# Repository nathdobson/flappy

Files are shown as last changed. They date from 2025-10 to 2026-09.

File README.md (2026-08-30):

# A 3d-printed Split Flap Display

This project is a redesign of David
Kingsman's [Split Flap Display](https://www.printables.com/model/69464-split-flap-display). See also the [product page](https://burntoutbakery.shop/).

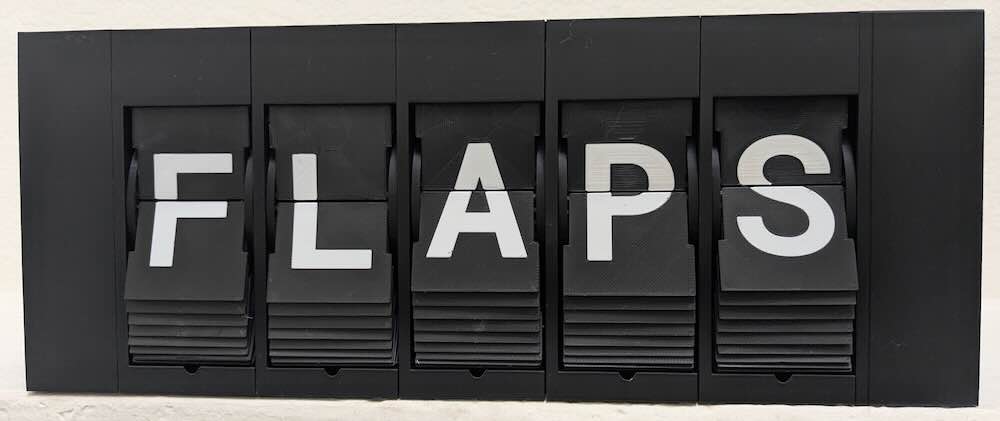
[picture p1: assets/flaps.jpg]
Split Flap Photo


## How it works

This display shows a sequence of symbols in individual 3d-printed modules. Each module contains a drum with flaps
displaying individual symbols. This is similar to a rolodex, except each symbol is split across the front of one flap
and the back of another flap. A motor rotates the drum to change from one symbol to another.

A client (e.g. [this webpage](https://flappy-7d77d.web.app/www)) sends messages to the microcontroller (MCU)
over [MQTT](https://mqtt.org/), a standardized publish/subscribe message protocol designed for IOT devices. Once the MCU
receives a message, it communicates with a series of daisy-chained motor driver circuit boards on the back of each
module. Each driver contains one shift register for controlling a unipolar stepper motor and one shift register for
reading a digital hall effect sensor. Each motor spins until a magnet on the drum activates the hall sensor, indicating
that the drum is at a particular absolute orientation. The motor then spins a specific number of steps to reach the
desired symbol.

## Prerequisites

Building this project from scratch requires a specific set of equipment and skills.

### Equipment

* Required

    * 3D printer with multi-material support (e.g. Bambu Labs A1 mini with AMS [^2]).
    * Device with a USB port capable of running Chrome.
    * [Soldering iron with temperature adjustment](https://www.amazon.com/Soldering-Digital-Welding-Portable-Electric/dp/B08R3515SF?th=1)
      for assembling boards and pushing Ruthex inserts into 3D printed parts.
    * Wire cutters
    * Wire strippers
    * Pliers
    * Allen wrenches

* Recommended

    * ["Dupont" crimping tool](https://www.amazon.com/IWISS-SN-28B-Crimping-AWG28-18-Dupont/dp/B00OMM4YUY?th=1) for
      assembling cables.
    * Multimeter for basic connection and voltage tests.

* Potentially useful
    * Laptop with at least 32GB of RAM for rendering models.
    * Oscilloscope for debugging serial communications.

### Skills

* Required
    * Soldering through-hole components
    * Crimping custom cables
* Recommended
    * The Rust programming language
    * Basic embedded software development
    * Basic understanding of CAD
    * Basic 3D printing debugging skills
    * Basic digital circuit design

## Bill of Materials

| Name of Part | Quantity per display | Quantity per letter | 
|---|---|---|
| [Raspberry Pi Pico 2 W MCU with headers](https://www.adafruit.com/product/6328) | 1 | |
| 12v power supply (at least 250mA per character) | 1 | |
| [Adafruit 12v to 5v converter](https://www.adafruit.com/product/5882) | 1 | |
| [Custom motor driver circuit board](https://github.com/nathdobson/flappy/tree/main/driver) | | 1 |
| [28BYJ-48 12v motor](https://www.amazon.com/Podazz-4-Phase-5-Line-Stepper-28BYJ-48/dp/B0DCFV3C2C) | | 1 |
| [KY-003 hall sensor module](https://www.amazon.com/Ransanx-Magnetic-KY-003-3-3V-5V-Pressure/dp/B0F32N1LHX?th=1) | | 1 |
| [PLA (background color)](https://us.store.bambulab.com/products/pla-basic-filament) | ~132 g | ~217 g |
| [PLA (foreground/text color)](https://us.store.bambulab.com/products/pla-basic-filament) | | ~18 g |
| [PETG](https://us.store.bambulab.com/products/petg-hf) for stacked prints (optional) | | ~30 g |
| Ruthex M2 inserts | 4 | 8 |
| Ruthex M3 inserts | 4 | 6 - 8 |
| [M2 x 6mm button head screws](https://www.amazon.com/dp/B0CNQXP56N?th=1) | 4 | 6 |
| [M2 x 10mm button head screws](https://www.amazon.com/dp/B0CNQVP8CC?th=1) | | 2 |
| [M3 x 6mm button head screws](https://www.amazon.com/dp/B0DNMZWZZV?th=1) | | 6 |
| [6mm x 2mm disc magnets](https://www.amazon.com/dp/B0CZ71S57Y?ref=ppx_yo2ov_dt_b_fed_asin_title&th=1) for drum | | 1 |
| Assorted dupont crimps, housings, and pin headers | | |
| [26 AWG UL1061 stranded wire](https://www.remingtonindustries.com/hook-up-wire/hook-up-wire-26-awg-ul1061-stranded-kit-2-color-sets-2-spool-sizes-available) for hall sensor cables | | |
| Assorted solid wire for manually soldered boards | | |
| Assorted stranded wire for cables | | |

## Repository structure

The repository is divided into several hardware and software components:

* [common/](common/) A cargo workspace with utilities and configuration in use by several components
* [driver/](driver/) A KiCad PCB design for the motor driver attached to each character.
* [firmware/](firmware/) A cargo workspace with the firmware for the Raspberry Pi Pico 2 W.
* [models/](models/) A cargo crate with binaries that generate .3mf files for each 3D-printed part.
* [native-client/](native-client/) A cargo workspace with a binary for configuring the display over USB or Bluetooth.
* [spindle/](spindle/) A cargo workspace with a simple scripting language for controlling the display.
* [submodules/](submodules/) A set of git submodules with forks of dependencies.
* [submodules/patina-rs](submodules/patina-rs/) A CAD library for generating 3D meshes from SDFs (signed distance
  functions).
* [web-client](web-client/) A WASM web application for interacting with the display.

## Instructions

### Hardware

1. Download the [latest release](https://github.com/nathdobson/flappy/releases/latest).
1. Order driver PCBs with JLCPCB:
    * `driver-jlcpcb-GERBER.zip` for producing the raw boards.
    * `driver-jlcpcb-BOM.csv` for ordering parts.
    * `driver-jlcpcb-CPL.csv` for placing and assembling parts.
1. For each module, print one each of the following:
    * `model-housing.3mf`: An enclosure for the module.
    * `model-inner.3mf`: The inner half of the drum.
    * `model-outer.3mf`: The outer half of the drum.
    * `model-flaps.3mf`: All flaps, stacked with PETG support. Ensure you have flow ratios tuned correctly for all
      filaments. This is effectively a 100% infill print, so overextrusion will ruin the top flaps. Underextrusion of
      the PLA will result in noticeable gaps. Underextrusion of the PETG support will ruin the surface quality of the
      PLA as it sinks into the gaps.
2. For each display, print one of the following:
    * `model-left-cap.3mf`: The cap for the left side of the display, where the motherboard goes.
    * `model-right-cap.3mf`: The cap for the right side of the display.
1. Press M2 and M3 Ruthex threaded inserts into the prints with a soldering iron.
1. Glue magnets into the inner drums. Ensure magnets are in the appropriate orientation for your sensors.
1. Connect inner and outer drums with screws.
1. Insert flaps into drum. PLA flaps should bend enough to fit in. Aligning the first letter with the magnet will
   simplify later calibration.
1. [Important] Remove the pull-up resistor or pull-up LED from the sensors[^1]. This is easy with flush cutters.
1. Route the motor and sensor cables through housings.
1. Connect all cables.
1. Connect the motors, sensors, and drivers to the housings with M2 and M3 screws. Ensure the motor tabs are properly
   centered on the supports.
1. Press the drum assemblies onto the motor axle. Ensure all flaps are pointed clockwise so they won't jam as the drum
   assembly rotates counter-clockwise.

### Software

1. Set up an MQTT broker (e.g. with https://www.emqx.com/).
1. Install the firmware by loading the [setup tool](https://flappy-7d77d.web.app/www/?tab=setup) in Chrome.
1. Fill out the settings in the setup tool. See [blank.json](native-client/blank.json) for defaults.
1. Enter the MQTT broker details in the [connect tool](https://flappy-7d77d.web.app/www/?tab=setup). You can use the resulting URL to connect to the display.
1. Adjust calibration values until the expected letters appear consistently.

## Controlling the display

### MQTT Protocol

In addition to controlling the display with the website, you may communicate directly with the display over MQTT. Each
display publishes or
subscribes to a set of topics with a common topic prefix.

#### Topic prefix + `"/info"`

The display publishes a `DeviceInfo` message (see [common/protocol/src/setup.rs](common/protocol/src/setup.rs)) on this
topic. This message is retained by the server, so new subscriptions to this topic will immediately receive this message.

#### Topic prefix + `"/request"`

Clients may publish `DisplayRequest` messages (see [common/protocol/src/display.rs](common/protocol/src/display.rs)) on
this
topic. If the display is processing a previous request when a new request arrives, the display cancels the previous
request and starts the new one.

##### `Run` messages

To display a single static message, send a UTF-8 encoded string as follows:

```
{"Run": "helloworld"}
```

The display splits the message into unicode graphemes, then tries to find the best match for each grapheme. The
algorithm accounts for [Unicode Equivalence](https://en.wikipedia.org/wiki/Unicode_equivalence) and capitalization.

##### `RunSpindle` messages

To display a repeating or changing message, send a UTF-8 encoded `spindle` script as follows:

```
{"RunSpindle": "display(\"hi\");sleep_ms(1000);display(\"hi\");"}
```

See the [Spindle](spindle/README.md) documentation for details on the scripting language.

#### Topic prefix + `"/response"`

When the display starts spinning the flaps to a new position, it sends a `Start` message with the content that will
appear. This message may not exactly match the original message due to normalization or capitalization changes.

```
{"Start":["H","E","L","L","O","W","O","R","L","D"]}
```

When the display stops spinning the flaps, it sends an equivalent `Stop` message:

```
{"Stop":["H","E","L","L","O","W","O","R","L","D"]}
```

The stop message is retained, so clients may determine the current contents of the display.

# License
The contents of the [models](models/) and [driver](driver/) directories and associated release artifacts
are licensed under the [CERN-OHL-W license](LICENSE-CERN-OHL-W-2.0). The remainder of this repository
is licensed under the [LGPL v3.0 license](LICENSE-LGPL-3.0).

[^2]: The provided 3MF files are configured for use with BambuStudio and tuned for PLA with PETG support on the Bambu A1 Mini
with AMS. The files will likely work on other slicers and printers, but may require additional tuning.

[^1]: The KY-003 board contains an A3144 digital hall sensor chip. The A3144 has a minimum Vcc of 4.5V and open-collector
active-low digital output. The KY-003 includes a resistor and LED in series to pull-up the output signal to Vcc. This
pull-up means the minimum logic output voltage for the KY-003 is also 4.5V. The
Pico's maximum logic voltage is 3.3V, so it cannot connect to a KY-003 without some extra work. Also, the LED introduces
a
voltage drop, which makes it's use as a pull-up in the first place questionable. Instead, we remove the pull-ups from
the KY-003, provide 12V to Vcc, and add a pull-up resistor to 3.3V on the driver board. Failure to remove the pull-ups
will likely result in damage to the driver boards.

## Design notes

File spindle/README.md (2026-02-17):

# Spindle

Spindle is a simple scripting language for controlling embedded systems.

## Features

* Rust-based syntax
* Imperative control flow
* Dynamic typing
* Reference-counted garbage collection
* [TODO] Incremental heap compaction to limit memory fragmentation
* Does not invoke the [global allocator](https://doc.rust-lang.org/std/alloc/index.html#the-global_allocator-attribute).
* Denial-of-service protection for untrusted scripts.
  * Memory usage limits
  * Compatible with `--cfg no_global_oom_handling`
  * Stack overflow protection
  * [TODO] Execution time budget between yields to the executor
* Compatible with `#![no_std]`.

## Types

* `i64` - a signed 64-bit integer.
* `bool` - false or true
* `null` - a type with the single value `null`
* `string` - a heap reference to a utf-8 encoded string

## Functions

* `display` - concatenates all parameters and show the resulting string on the display,
  returning once the flaps stop spinning.
  ```
  display("HelloWorld");
  ```
* `print` - print a string to the serial console.
* `sleep_ms` - wait for a certain number of milliseconds to pass.
  ```
  display("Hello");
  sleep_ms(1000);
  display("Bye");
  ```

## Language features
* String literals with double quotes: (e..g `"helloworld"`
* Integer literals (e.g. `10`)
* `null` literal
* boolean literals `false` and `true`.
* Arithmetic operators on integers `+`, `-`, `*`, `/`.
* Variables with declarations with `let` statements.
  ```
  let x = 1;
  display(x);
  ```
* `if` and `if`-`else` statements
    ```
    if foo {
        ...
    }
    ```
    ```
    if foo {
        ...
    } else {
        ....
    }
    ```
    ```
    if foo {
        ...
    } else if bar {
        ...
    } else {
        ...
    }
    ```
* `for` range loops (first index is inclusive, second index is exclusive).
    ```
    for x in 0..10 {
        print(x);
    }
    ```

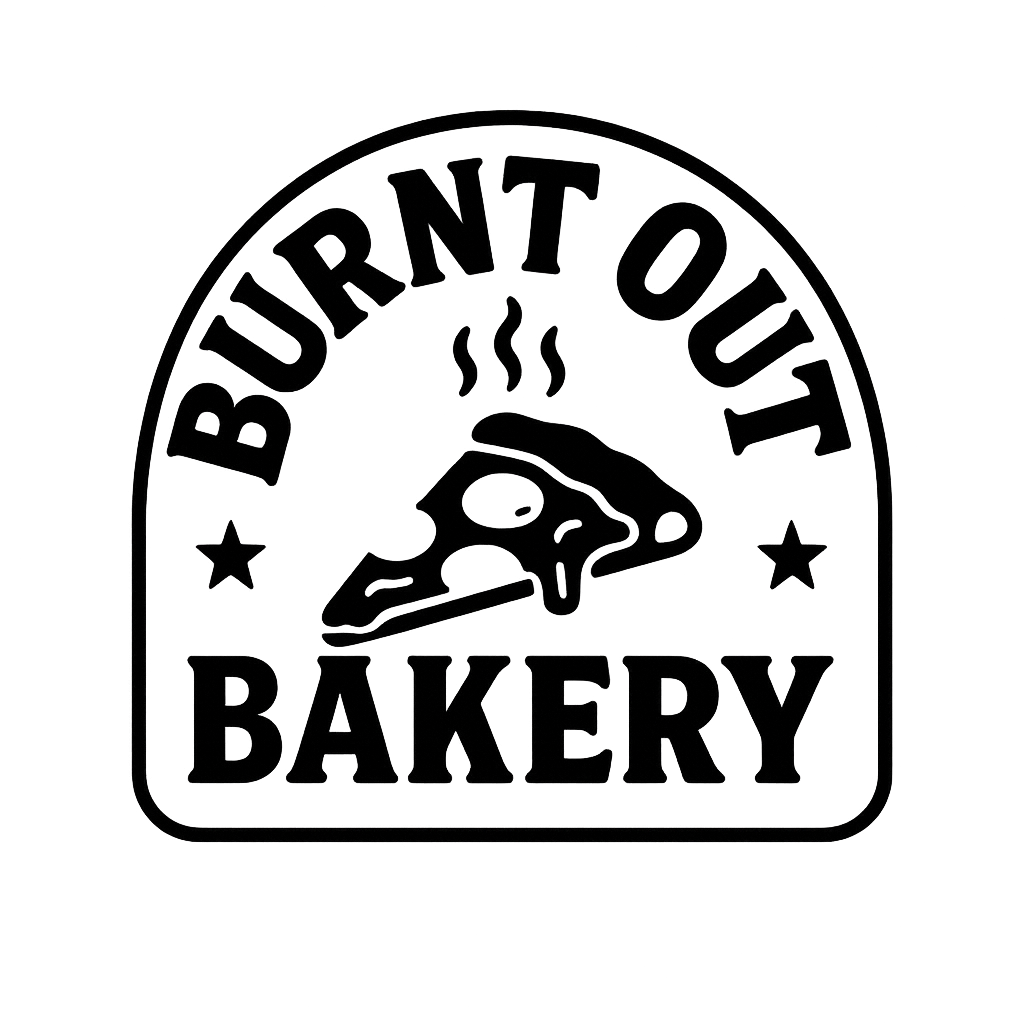
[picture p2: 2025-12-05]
driver/driver-v4/BurntOutBakery/BurntOutBakery.png

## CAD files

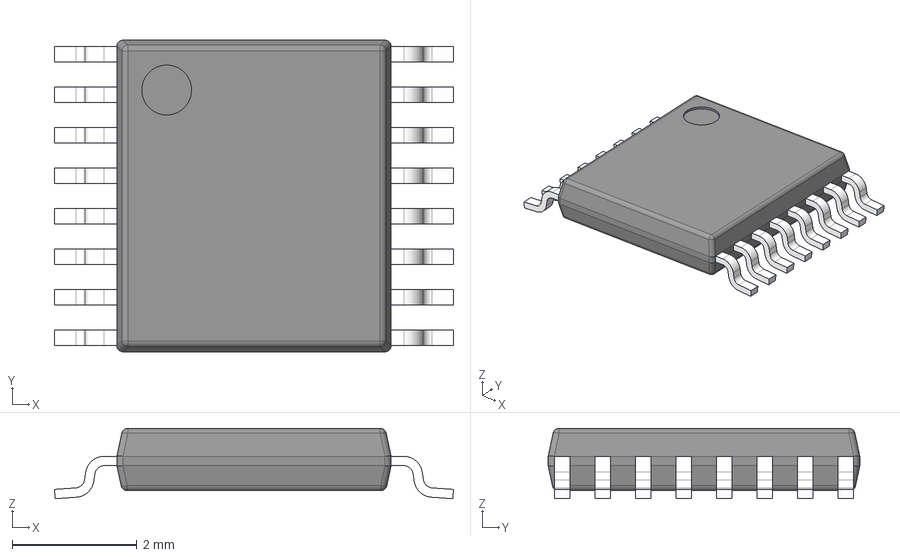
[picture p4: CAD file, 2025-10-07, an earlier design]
driver/driver-v2/ul_DRV8804PWP/PWP0016J.stp
6.40 x 5.00 x 1.13 mm
BODY-TSSOP
LEAD-TSSOP x 16
PIN1
DAP

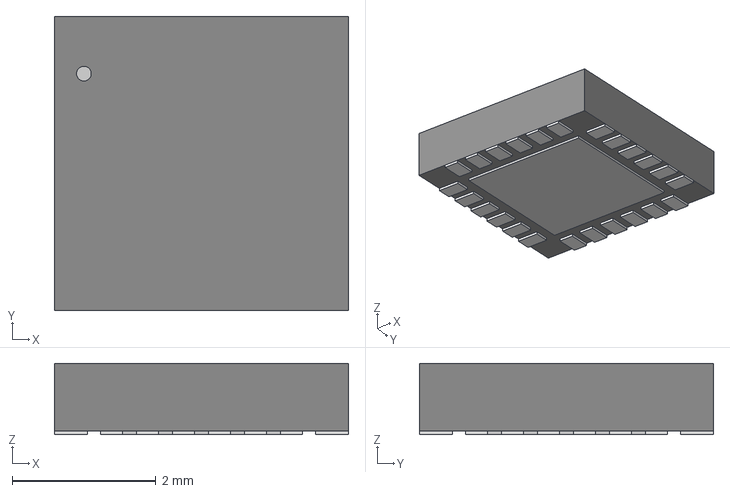
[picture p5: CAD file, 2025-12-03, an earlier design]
driver/driver-v2/ul_MP6605CGR-Z/QFN-24_MP6605C_MNP.step
4.09 x 4.09 x 0.993 mm

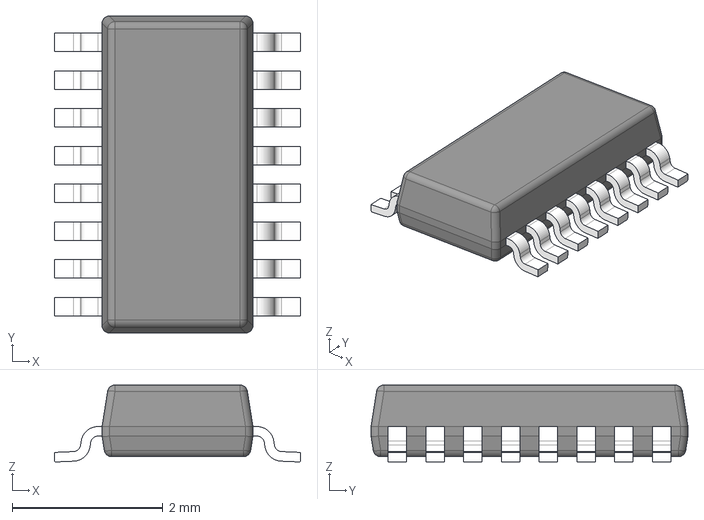
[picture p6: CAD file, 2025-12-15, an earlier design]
driver/driver-v2/ul_SN74HCS165DYYR/DYY0016A.stp
3.26 x 4.20 x 1.02 mm
BODY-TSSOP
LEAD-TSSOP x 16

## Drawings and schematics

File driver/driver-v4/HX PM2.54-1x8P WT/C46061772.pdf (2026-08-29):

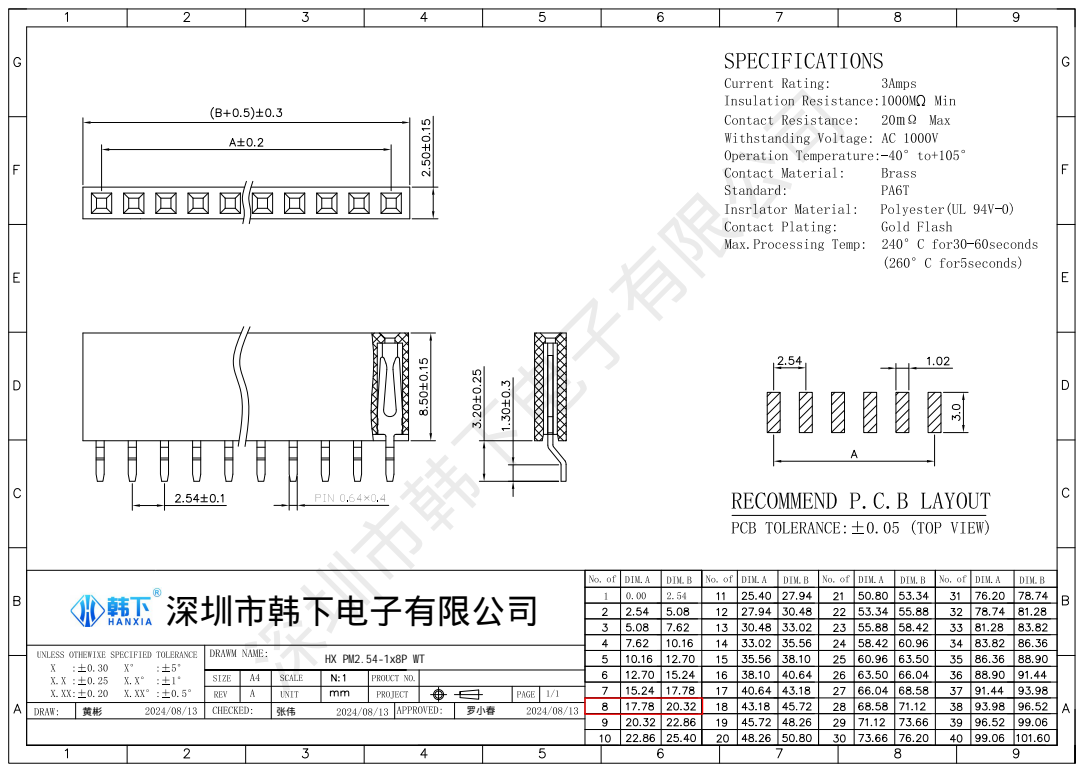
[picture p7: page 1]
深圳市韩下电子有限公司

深圳市韩下电子有限公司 HX PM2.54-1x8P WT 罗小春

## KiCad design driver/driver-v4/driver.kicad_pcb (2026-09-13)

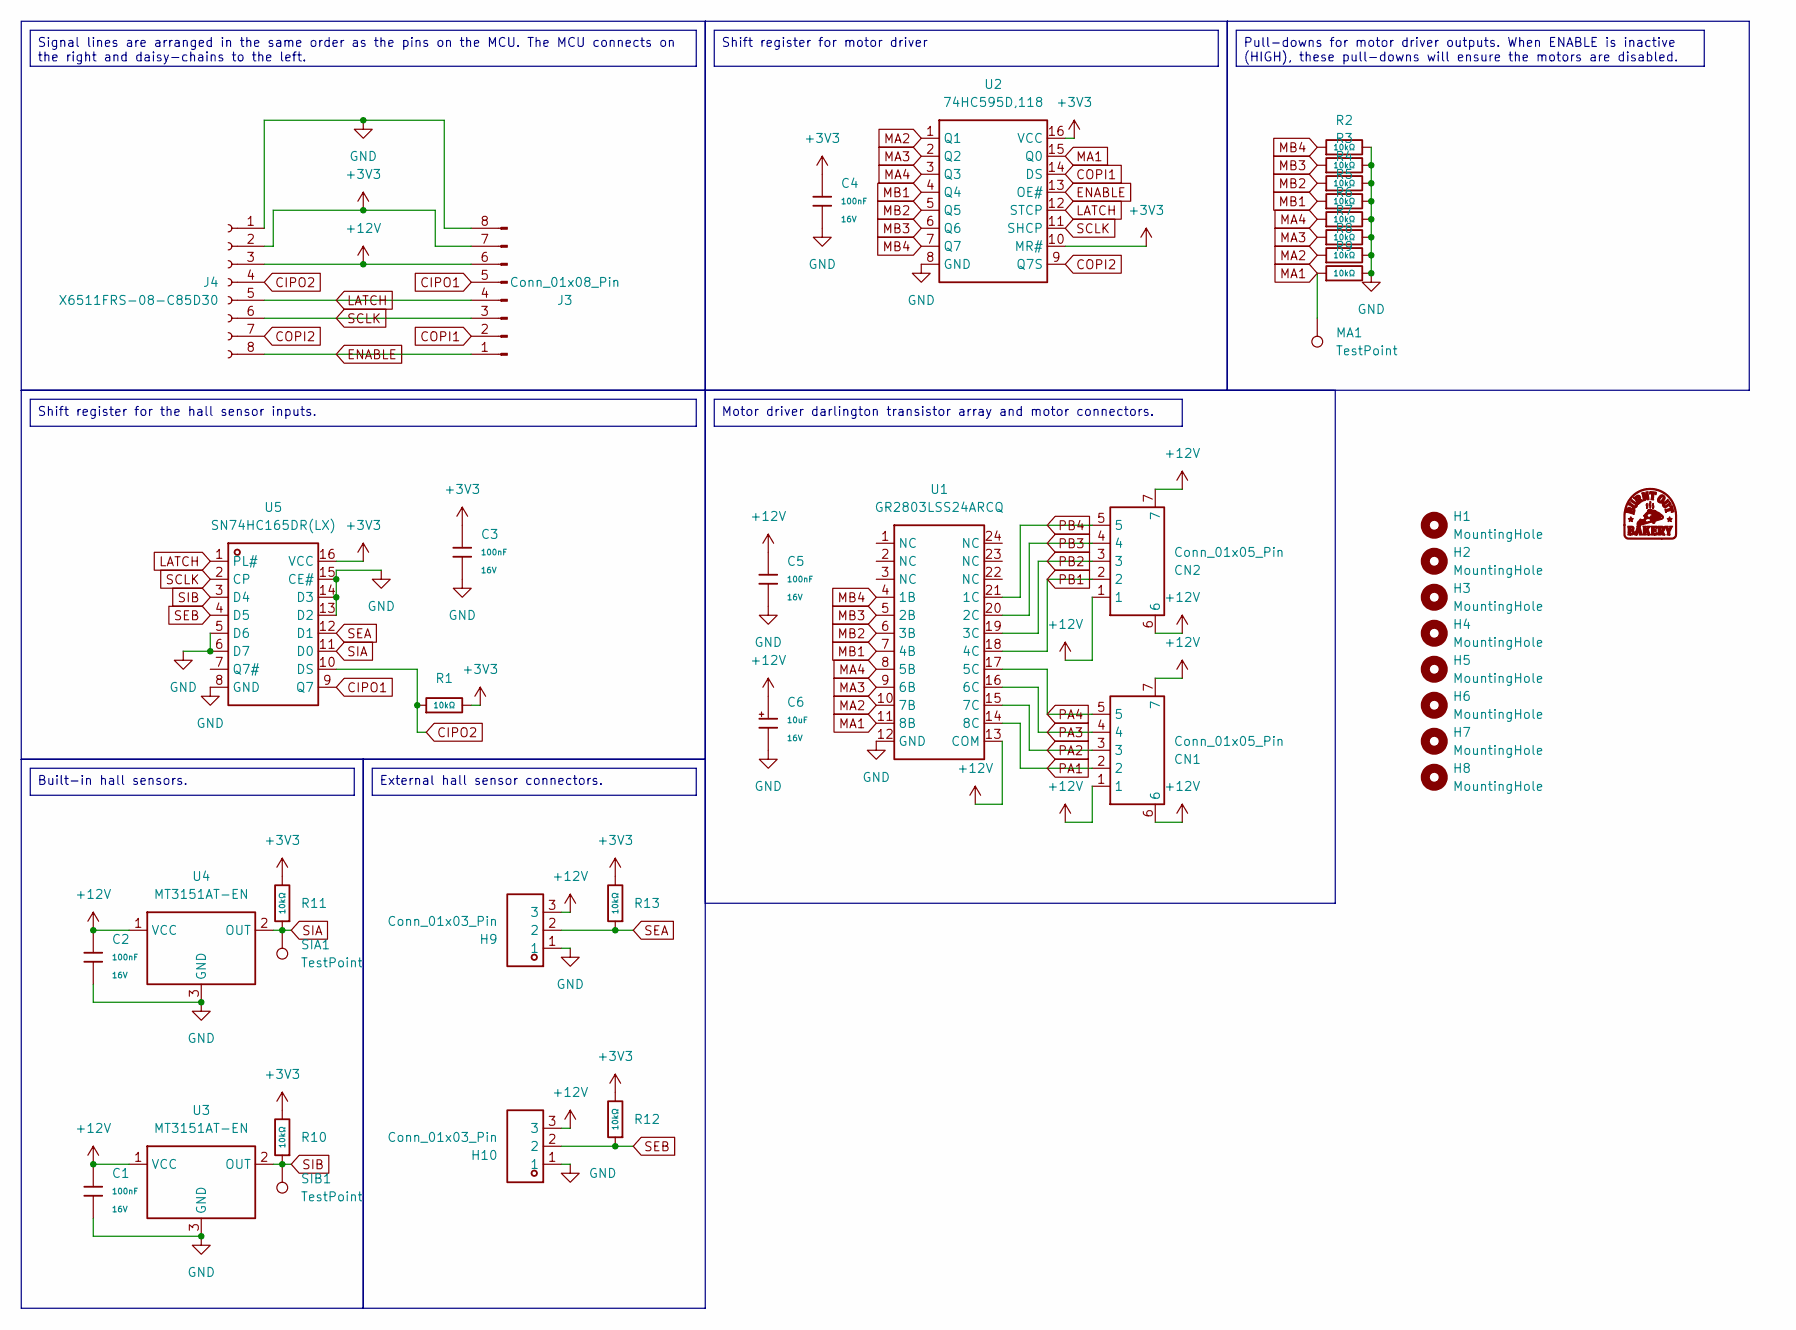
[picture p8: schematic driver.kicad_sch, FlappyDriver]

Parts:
C1, C2, C3, C4, C5: 100nF; C_0402; Voltage Rated 16V; Tolerance ±10%; Part CL05B104KO5NNNC; LCSC C1525
C6: 10uF; C_CASE-A-3216-18(mm); Tolerance ±10%; Rated Voltage 16V; Part TAJA106K016RNJ; LCSC C7171
CN1, CN2: Conn_01x05_Pin; CONN-SMD_5P-P2.50_2.54-5P-LT; Manufacturer Part 2.54-5P-LT; LCSC Part Name 1x5P 间距:2.5mm 立贴 系列:XH
G1: LOGO; BurntOutBakery
H1, H2, H3, H4, H5, H6, H7, H8: MountingHole; MountingHole_2.2mm_M2_ISO14580
H9, H10: Conn_01x03_Pin; HDR-TH_3P-P2.54_DZ254S-11-03-48; Manufacturer Part DZ254S-11-03-48; LCSC Part Name 1x3P 间距:2.54mm 方针 立贴
J3: Conn_01x08_Pin; HDR-SMD_PZ254RS-11-08P-01
J4: X6511FRS-08-C85D30; HDR-SMD_8P-P2.54-H-F-L11.5
MA1: TestPoint; TestPoint_THTPad_D2.0mm_Drill1.0mm
R1, R2, R3, R4, R5, R6, R7, R8, R9, R10, R11, R12, R13: 10kΩ; R_0402; Overload Voltage (Max) 50V; Tolerance ±1%; Part 0402WGF1002TCE; LCSC C25744
SIA1: TestPoint; TestPoint_THTPad_D2.0mm_Drill1.0mm
SIB1: TestPoint; TestPoint_THTPad_D2.0mm_Drill1.0mm
U1: GR2803LSS24ARCQ; SSOP-24_L8.7-W3.9-P0.64-LS6.0-BL; Manufacturer Part GR2803LSS24ARCQ; LCSC Part Name 通道数: 8 集射击穿电压: 25V 集电极电流：500mA 最大输入电压：1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
U2: 74HC595D,118; SOIC-16_L9.9-W3.9-P1.27-LS6.0-BL; Manufacturer Part 74HC595D,118; LCSC Part Name 三态输出 串行至串行或并行移位寄存器
U3, U4: MT3151AT-EN; SOT-23-3_L2.9-W1.3-P1.90-LS2.4-BR; Manufacturer Part MT3151AT-EN; LCSC Part Name 单极检测芯片
U5: SN74HC165DR(LX); SOP-16_L10.0-W3.9-P1.27-LS6.0-BL; Manufacturer Part SN74HC165DR(LX); LCSC Part Name 集成电路

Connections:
+3V3: C3.1, C4.1, J3.7, J4.2, R1.2, R10.2, R11.2, R12.2, R13.2, U2.10 (MR#), U2.16 (VCC), U5.16 (VCC)
+12V: C1.1, C2.1, C5.1, C6.1, CN1.1, CN1.6, CN1.7, CN2.1, CN2.6, CN2.7, H9.3, H10.3, J3.6, J4.3, U1.13 (COM), U3.1 (VCC), U4.1 (VCC)
CIPO1: J3.5, U5.9 (Q7)
CIPO2: J4.4, R1.1, U5.10 (DS)
COPI1: J3.2, U2.14 (DS)
COPI2: J4.7, U2.9 (Q7S)
ENABLE: J3.1, J4.8, U2.13 (OE#)
GND: C1.2, C2.2, C3.2, C4.2, C5.2, C6.2, H9.1, H10.1, J3.8, J4.1, R2.2, R3.2, R4.2, R5.2, R6.2, R7.2, R8.2, R9.2, U1.12 (GND), U2.8 (GND), U3.3 (GND), U4.3 (GND), U5.5 (D6), U5.6 (D7), U5.8 (GND), U5.13 (D2), U5.14 (D3), U5.15 (CE#)
LATCH: J3.4, J4.5, U2.12 (STCP), U5.1 (PL#)
MA1: MA1.1, R9.1, U1.11 (8B), U2.15 (Q0)
MA2: R8.1, U1.10 (7B), U2.1 (Q1)
MA3: R7.1, U1.9 (6B), U2.2 (Q2)
MA4: R6.1, U1.8 (5B), U2.3 (Q3)
MB1: R5.1, U1.7 (4B), U2.4 (Q4)
MB2: R4.1, U1.6 (3B), U2.5 (Q5)
MB3: R3.1, U1.5 (2B), U2.6 (Q6)
MB4: R2.1, U1.4 (1B), U2.7 (Q7)
PA1: CN1.2, U1.14 (8C)
PA2: CN1.3, U1.15 (7C)
PA3: CN1.4, U1.16 (6C)
PA4: CN1.5, U1.17 (5C)
PB1: CN2.2, U1.18 (4C)
PB2: CN2.3, U1.19 (3C)
PB3: CN2.4, U1.20 (2C)
PB4: CN2.5, U1.21 (1C)
SCLK: J3.3, J4.6, U2.11 (SHCP), U5.2 (CP)
SEA: H9.2, R13.1, U5.12 (D1)
SEB: H10.2, R12.1, U5.4 (D5)
SIA: R11.1, SIA1.1, U4.2 (OUT), U5.11 (D0)
SIB: R10.1, SIB1.1, U3.2 (OUT), U5.3 (D4)

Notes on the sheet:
Shift register for the hall sensor inputs.
Signal lines are arranged in the same order as the pins on the MCU. The MCU connects on the right and daisy-chains to the left.
Pull-downs for motor driver outputs. When ENABLE is inactive (HIGH), these pull-downs will ensure the motors are disabled.
Built-in hall sensors.
External hall sensor connectors.
Motor driver darlington transistor array and motor connectors.
Shift register for motor driver

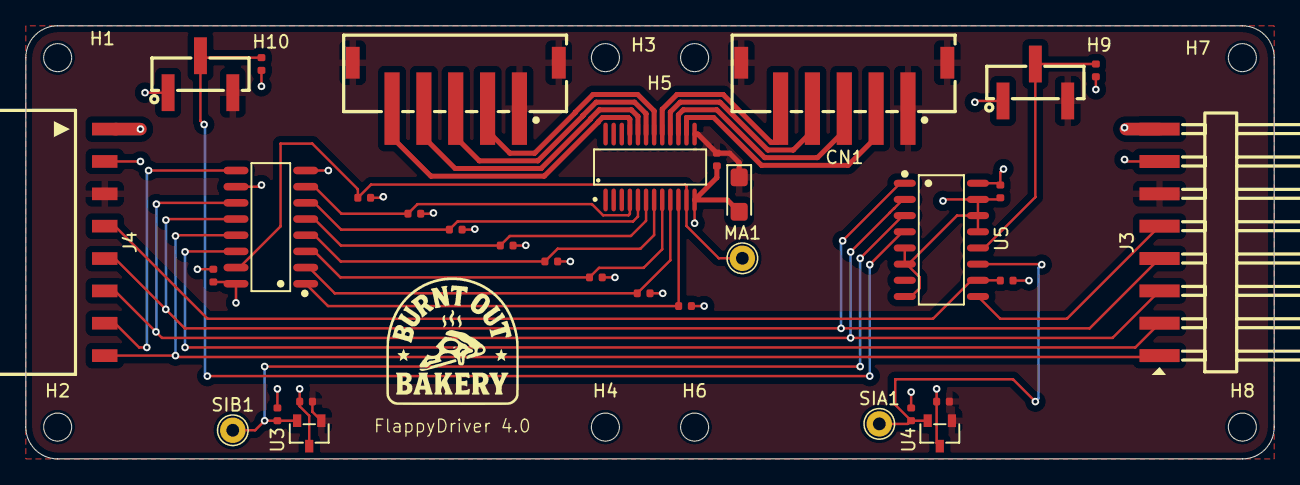
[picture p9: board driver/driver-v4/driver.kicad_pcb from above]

Board: 4 copper layers, 98.0 x 34.0 mm, 42 parts (0 on the bottom side), 30 nets.

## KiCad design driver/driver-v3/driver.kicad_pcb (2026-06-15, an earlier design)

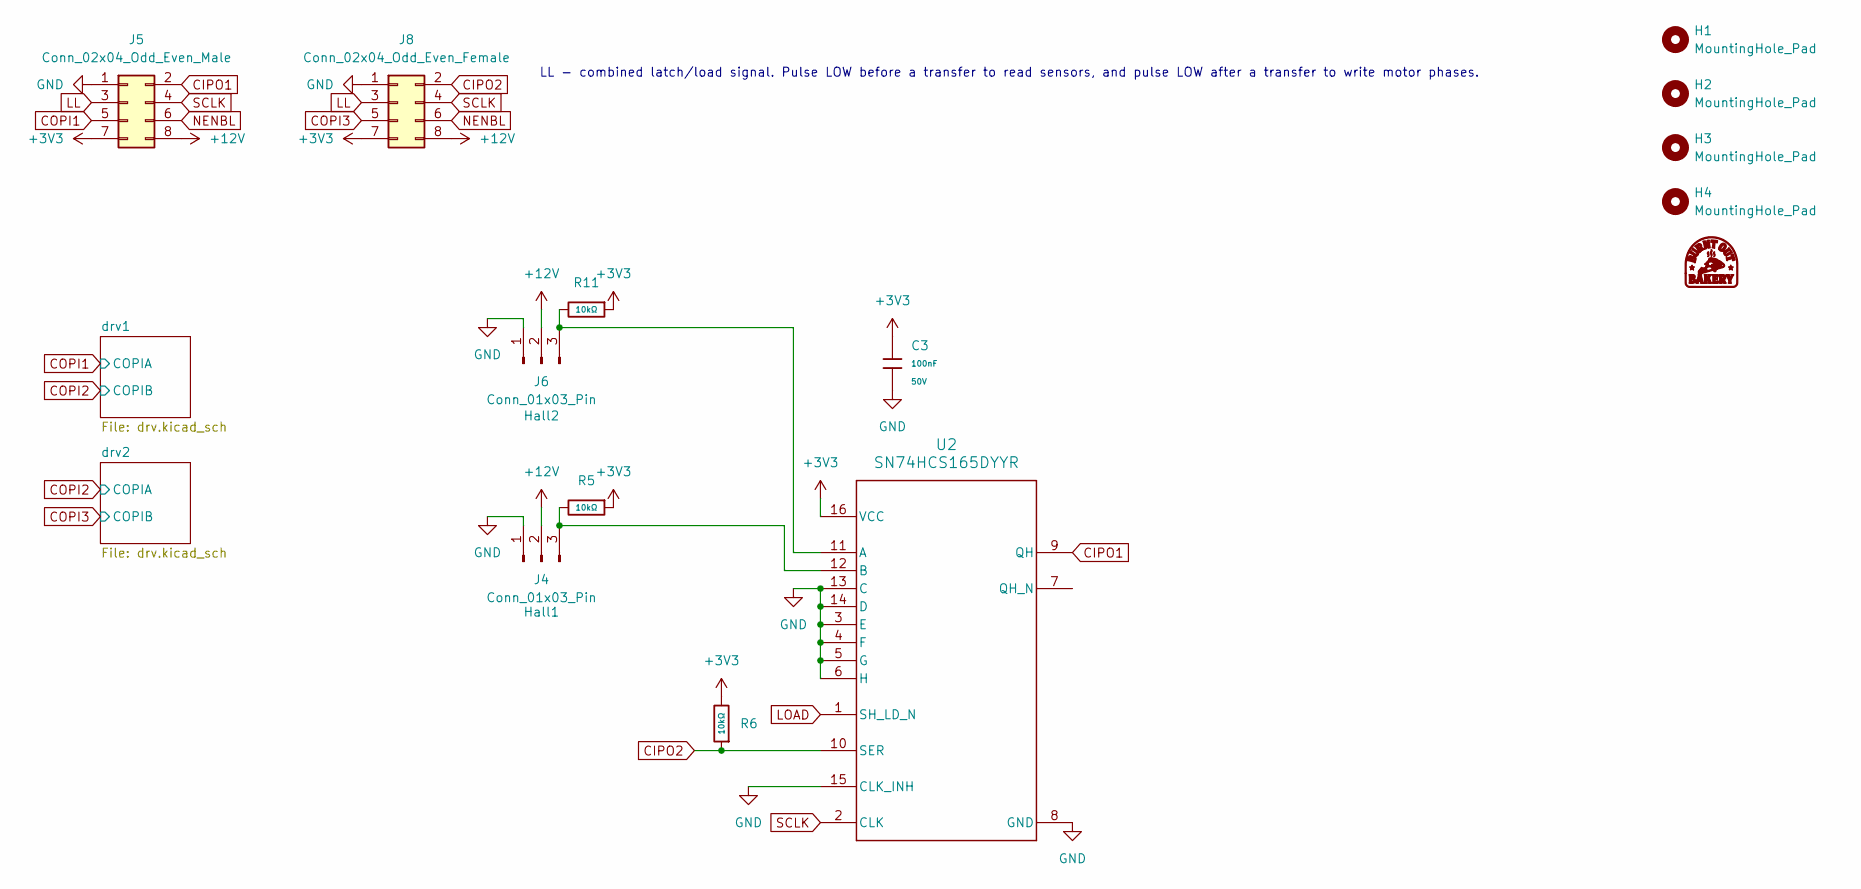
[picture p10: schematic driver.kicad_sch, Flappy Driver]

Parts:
C3: 100nF; C_0603; Voltage Rated 50V; Tolerance ±10%; Part CC0603KRX7R9BB104; LCSC C14663
G1: LOGO; BurntOutBakery
H1, H2, H3, H4: MountingHole_Pad; MountingHole_2.2mm_M2_ISO14580
J4, J6: Conn_01x03_Pin; PinHeader_1x03_P2.54mm_Vertical
J5: Conn_02x04_Odd_Even_Male; PinHeader_2x04_P2.54mm_Horizontal
J8: Conn_02x04_Odd_Even_Female; PinSocket_2x04_P2.54mm_Horizontal
R5, R6, R11: 10kΩ; R_0402; Overload Voltage (Max) 50V; Tolerance ±1%; Part 0402WGF1002TCE; LCSC C25744
U2: SN74HCS165DYYR; DYY0016A-MFG

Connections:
+3V3: C3.1, J5.7, J8.7, R5.1, R6.2, R11.1, U2.16 (VCC)
+12V: J4.2, J5.8, J6.2, J8.8; also elsewhere on the board
CIPO1: J5.2, U2.9 (QH)
CIPO2: J8.2, R6.1, U2.10 (SER)
COPI1: J5.5; also elsewhere on the board
COPI3: J8.5; also elsewhere on the board
GND: C3.2, J4.1, J5.1, J6.1, J8.1, U2.3 (E), U2.4 (F), U2.5 (G), U2.6 (H), U2.8 (GND), U2.13 (C), U2.14 (D), U2.15 (CLK_INH); also elsewhere on the board
LL: J5.3, J8.3
LOAD: U2.1 (SH_LD_N)
NENBL: J5.6, J8.6; also elsewhere on the board
unnamed: J4.3, R5.2, U2.12 (B)
unnamed: J6.3, R11.2, U2.11 (A)
SCLK: J5.4, J8.4, U2.2 (CLK); also elsewhere on the board

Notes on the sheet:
LL - combined latch/load signal. Pulse LOW before a transfer to read sensors, and pulse LOW after a transfer to write motor phases.

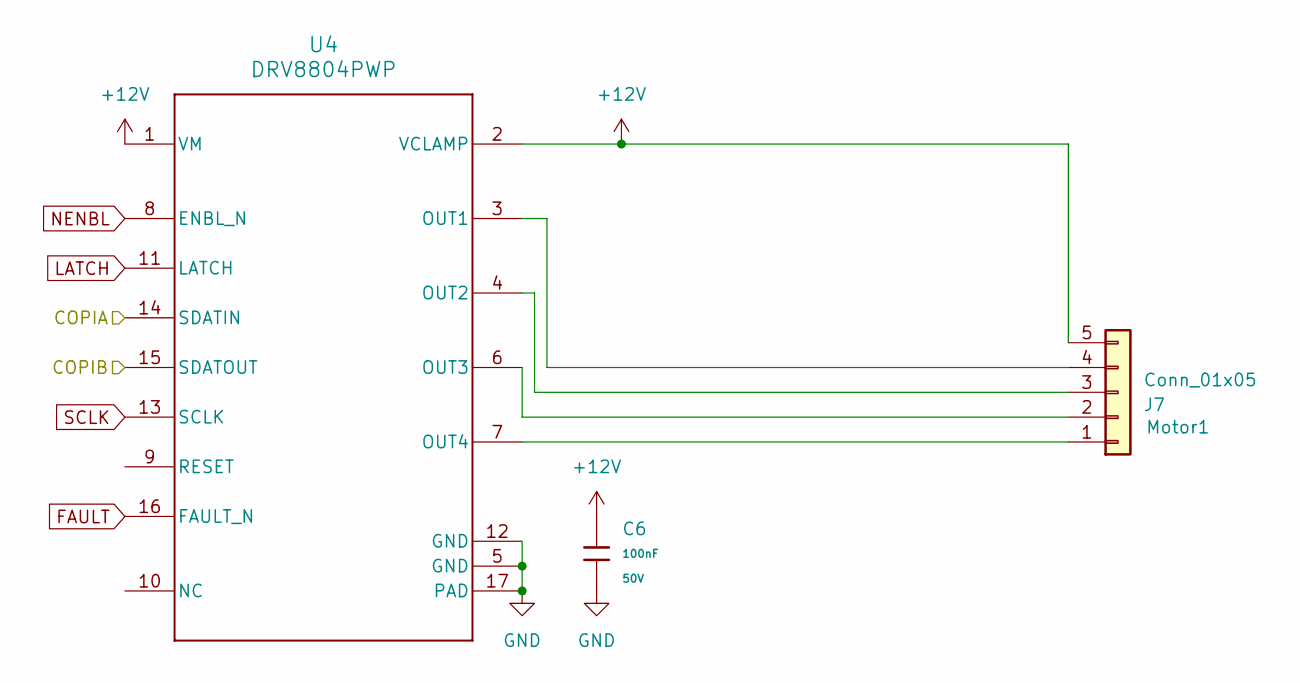
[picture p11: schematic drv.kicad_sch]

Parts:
C6: 100nF; C_0603; Voltage Rated 50V; Tolerance ±10%; Part CC0603KRX7R9BB104; LCSC C14663
J7: Conn_01x05; JST_XH_B5B-XH-A_1x05_P2.50mm_Vertical
U4: DRV8804PWP; HTSSOP-16-1EP_4.4x5mm_P0.65mm_EP3.4x5mm_Mask3x3mm_ThermalVi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

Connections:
+12V: C6.1, J7.5, U4.1 (VM), U4.2 (VCLAMP); also elsewhere on the board
COPI1: U4.14 (SDATIN); also elsewhere on the board
COPI2: U4.15 (SDATOUT); also elsewhere on the board
FAULT: U4.16 (FAULT_N); also elsewhere on the board
GND: C6.2, U4.5 (GND), U4.12 (GND), U4.17 (PAD); also elsewhere on the board
LATCH: U4.11 (LATCH); also elsewhere on the board
NENBL: U4.8 (ENBL_N); also elsewhere on the board
unnamed: J7.1, U4.7 (OUT4)
unnamed: J7.2, U4.6 (OUT3)
unnamed: J7.3, U4.4 (OUT2)
unnamed: J7.4, U4.3 (OUT1)
SCLK: U4.13 (SCLK); also elsewhere on the board

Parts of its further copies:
C1: 100nF; C_0603; Voltage Rated 50V; Tolerance ±10%; Part CC0603KRX7R9BB104; LCSC C14663
J3: Conn_01x05; JST_XH_B5B-XH-A_1x05_P2.50mm_Vertical
U1: DRV8804PWP; HTSSOP-16-1EP_4.4x5mm_P0.65mm_EP3.4x5mm_Mask3x3mm_ThermalVi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

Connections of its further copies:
+12V: C1.1, J3.5, U1.1 (VM), U1.2 (VCLAMP); also elsewhere on the board
COPI2: U1.14 (SDATIN); also elsewhere on the board
COPI3: U1.15 (SDATOUT); also elsewhere on the board
FAULT: U1.16 (FAULT_N); also elsewhere on the board
GND: C1.2, U1.5 (GND), U1.12 (GND), U1.17 (PAD); also elsewhere on the board
LATCH: U1.11 (LATCH); also elsewhere on the board
NENBL: U1.8 (ENBL_N); also elsewhere on the board
unnamed: J3.1, U1.7 (OUT4)
unnamed: J3.2, U1.6 (OUT3)
unnamed: J3.3, U1.4 (OUT2)
unnamed: J3.4, U1.3 (OUT1)
SCLK: U1.13 (SCLK); also elsewhere on the board

Board: 2 copper layers, 20 parts (0 on the bottom side), 23 nets, no tracks yet.

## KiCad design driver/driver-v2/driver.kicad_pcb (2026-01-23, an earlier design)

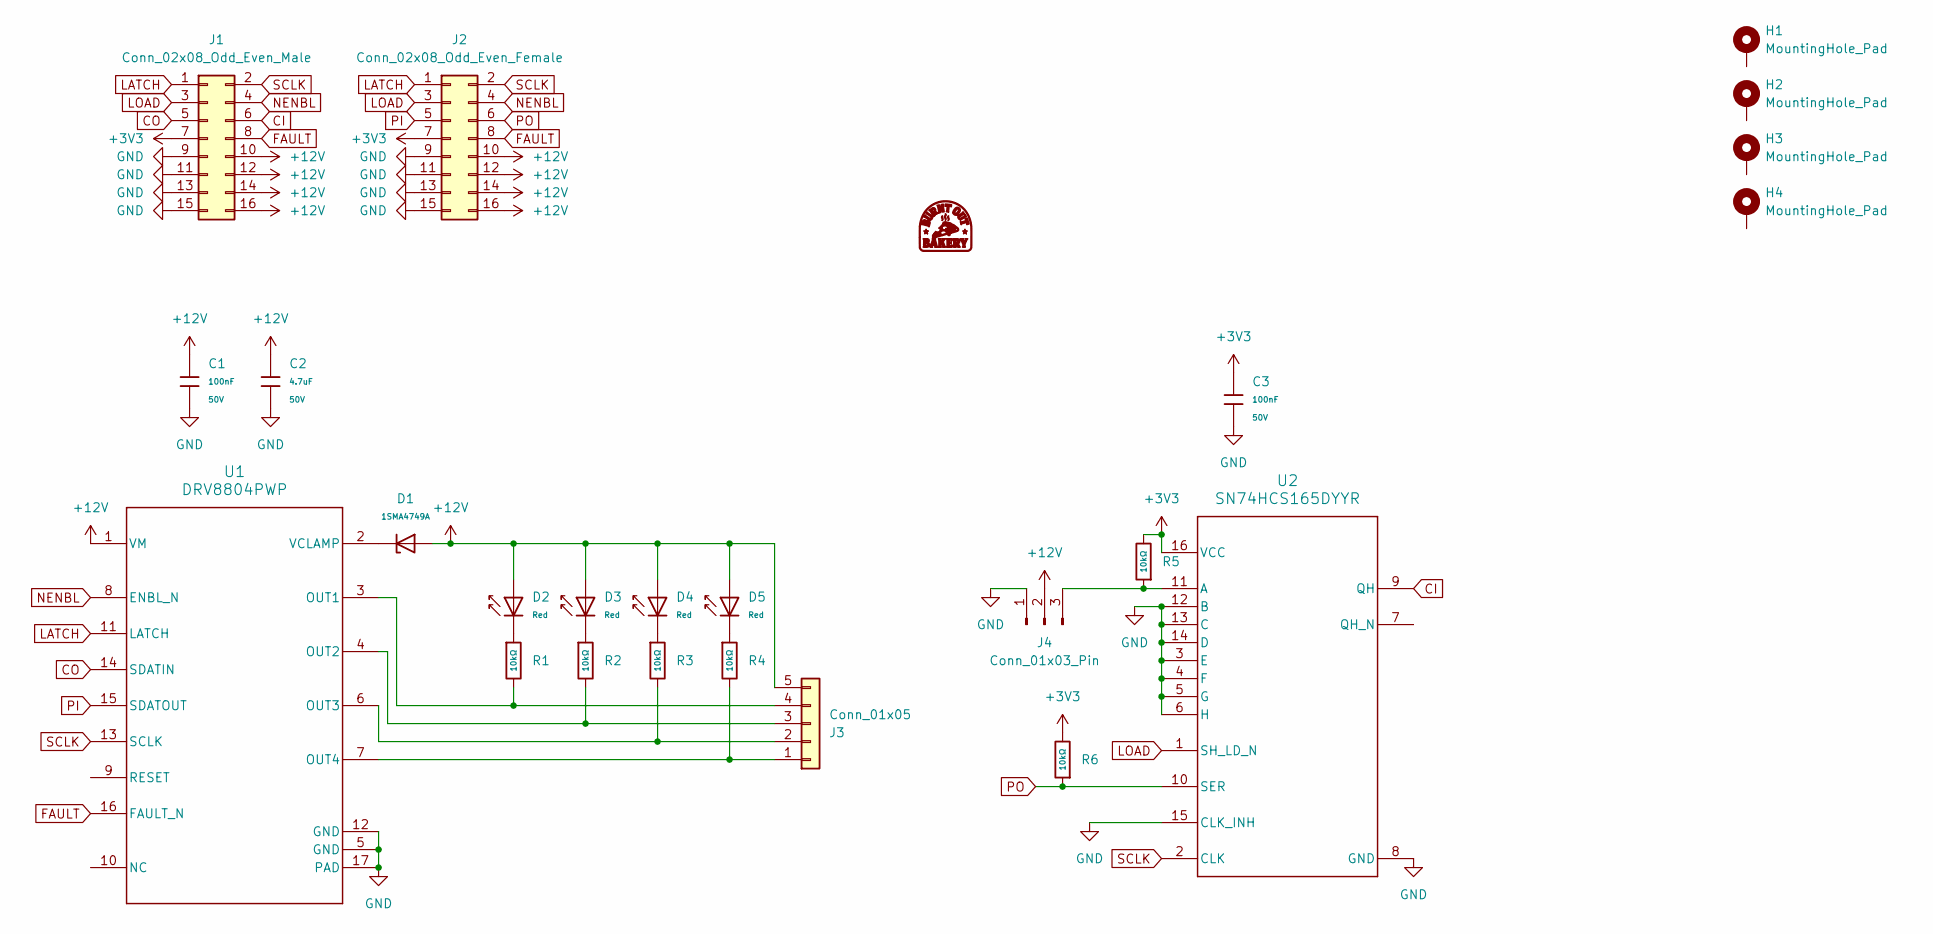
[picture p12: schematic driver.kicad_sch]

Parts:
C1, C3: 100nF; C_0603; Voltage Rated 50V; Tolerance ±10%; Part CC0603KRX7R9BB104; LCSC C14663
C2: 4.7uF; C_1206; Voltage Rated 50V; Tolerance ±10%; Part 1206B475K500NT; LCSC C29823
D1: 1SMA4749A; D_DO-214AC(SMA); Part 1SMA4749A; LCSC C19077485
D2, D3, D4, D5: Red; D_0603; Part KT-0603R; LCSC C2286
G1: LOGO; BurntOutBakery
H1, H2, H3, H4: MountingHole_Pad; MountingHole_2.2mm_M2_ISO14580_Pad
J1: Conn_02x08_Odd_Even_Male; PinHeader_2x08_P2.54mm_Horizontal
J2: Conn_02x08_Odd_Even_Female; PinSocket_2x08_P2.54mm_Horizontal
J3: Conn_01x05; JST_XH_B5B-XH-A_1x05_P2.50mm_Vertical
J4: Conn_01x03_Pin; PinHeader_1x03_P2.54mm_Vertical
R1, R2, R3, R4, R5, R6: 10kΩ; R_0402; Overload Voltage (Max) 50V; Tolerance ±1%; Part 0402WGF1002TCE; LCSC C25744
U1: DRV8804PWP; HTSSOP-16-1EP_4.4x5mm_P0.65mm_EP3.4x5mm_Mask3x3mm_ThermalVi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
U2: SN74HCS165DYYR; DYY0016A-MFG

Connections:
+3V3: C3.1, J1.7, J2.7, R5.2, R6.2, U2.16 (VCC)
+12V: C1.1, C2.1, D1.2, D2.2, D3.2, D4.2, D5.2, J1.10, J1.12, J1.14, J1.16, J2.10, J2.12, J2.14, J2.16, J3.5, J4.2, U1.1 (VM)
CI: J1.6, U2.9 (QH)
CO: J1.5, U1.14 (SDATIN)
FAULT: J1.8, J2.8, U1.16 (FAULT_N)
GND: C1.2, C2.2, C3.2, J1.9, J1.11, J1.13, J1.15, J2.9, J2.11, J2.13, J2.15, J4.1, U1.5 (GND), U1.12 (GND), U1.17 (PAD), U2.3 (E), U2.4 (F), U2.5 (G), U2.6 (H), U2.8 (GND), U2.12 (B), U2.13 (C), U2.14 (D), U2.15 (CLK_INH)
LATCH: J1.1, J2.1, U1.11 (LATCH)
LOAD: J1.3, J2.3, U2.1 (SH_LD_N)
NENBL: J1.4, J2.4, U1.8 (ENBL_N)
unnamed: D2.1, R1.1
unnamed: D3.1, R2.1
unnamed: D4.1, R3.1
unnamed: D5.1, R4.1
unnamed: J3.1, R4.2, U1.7 (OUT4)
unnamed: J3.2, R3.2, U1.6 (OUT3)
unnamed: J3.3, R2.2, U1.4 (OUT2)
unnamed: J3.4, R1.2, U1.3 (OUT1)
unnamed: J4.3, R5.1, U2.11 (A)
unnamed: D1.1, U1.2 (VCLAMP)
PI: J2.5, U1.15 (SDATOUT)
PO: J2.6, R6.1, U2.10 (SER)
SCLK: J1.2, J2.2, U1.13 (SCLK), U2.2 (CLK)

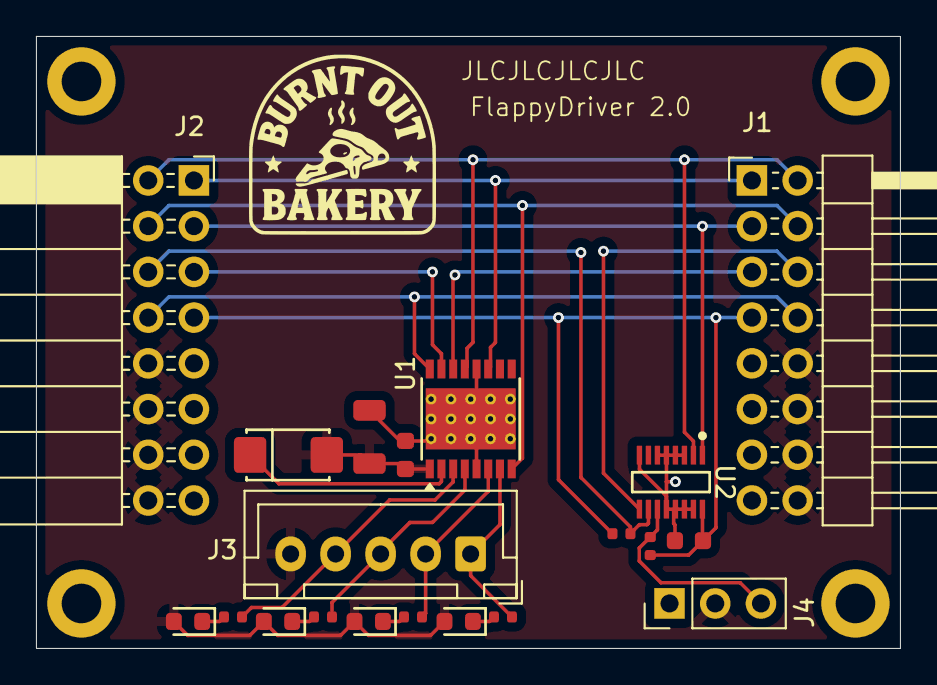
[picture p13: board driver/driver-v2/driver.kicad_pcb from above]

Board: 2 copper layers, 48.0 x 34.0 mm, 25 parts (0 on the bottom side), 22 nets.

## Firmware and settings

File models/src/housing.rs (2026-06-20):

#![deny(unused_must_use)]
#![allow(unused_mut)]
#![allow(dead_code)]
#![allow(unused_imports)]

use crate::tabs::Tabs;
use anyhow::Context;
use models::encode_sdf::EncodeBuilder;
use patina_3mf::brim_points::BrimPoint;
use patina_3mf::project_settings::brim_type::BrimType;
use patina_bambu::BambuBuilder;
use patina_bambu::model::SdfModel;
use patina_geo::aabb::Aabb;
use patina_geo::geo2::polygon2::Polygon2;
use patina_geo::geo2::triangle2::Triangle2;
use patina_geo::geo3::aabb3::Aabb3;
use patina_geo::geo3::cylinder::Cylinder;
use patina_geo::geo3::plane::Plane;
use patina_geo::geo3::triangle3::Triangle3;
use patina_geo::sphere::Circle;
use patina_mesh::decimate::Decimate;
use patina_mesh::half_edge_mesh::HalfEdgeMesh;
use patina_mesh::mesh::Mesh;
use patina_mesh::ser::encode_file;
use patina_sdf::marching_mesh::MarchingMesh;
use patina_sdf::sdf::leaf::SdfLeafImpl;
use patina_sdf::sdf::truncated_cone::TruncatedCone;
use patina_sdf::sdf::{AsSdf, Sdf, Sdf3};
use patina_threads::{THREAD_M2, THREAD_M3, ThreadMetrics};
use patina_vec::mat4::Mat4;
use patina_vec::vec2::Vec2;
use patina_vec::vec3::Vec3;
use std::f64;
use std::path::Path;
use std::time::Instant;

mod tabs;

struct Catch {
    bottom_y: f64,
    indent_x: f64,
}

struct Mount {
    off_x: f64,
    off_y: f64,
    length: f64,
    motor_radius: f64,
    motor_fit: f64,
    rad1: f64,
    rad2: f64,
    extra_back: f64,
}

struct Brace {
    width: f64,
    extent: f64,
    indent: f64,
}

struct Port {
    start_x: f64,
    width: f64,
    length: f64,
}

struct HallPort {
    start_x: f64,
    start_y: f64,
    width: f64,
    length: f64,
}

struct Tube {
    width: f64,
    wall_bottom: f64,
    wall_top: f64,
    wire_inlet1: f64,
    wire_inlet2: f64,
    tab_width: f64,
}

struct HallMount {
    width: f64,
    thickness: f64,
    length: f64,

    hole1_x: f64,
    off_y: f64,
    rad1: f64,
    rad2: f64,
    tilt_deg: f64,
    extra_cone: f64,
    hole_bias: f64,
}

struct DrumGuide {
    length: f64,
    rad_inner: f64,
    rad_outer: f64,
    seam_cut_width: f64,
    seam_cut_depth: f64,
}

struct BoardMounts {
    standoff: f64,
    thread: &'static ThreadMetrics,
    brace_width: f64,
    brace_inset: f64,
    board1_vertical: f64,
    board2_vertical: f64,
    board_width: f64,
    board_height: f64,
    board_offset_z: f64,
}
struct HousingBuilder {
    aabb: Aabb3,
    inf: f64,
    drum_bounding_radius: f64,
    back_thickness: f64,
    catch: Catch,
    mount: Mount,
    brace: Brace,
    port: Port,
    hall_port: HallPort,
    tabs: Tabs,
    tube: Tube,
    hall_mount: HallMount,
    drum_guide: DrumGuide,
    top_catch: TopCatch,
    board_mounts: BoardMounts,
    vertical_mounts: VerticalMounts,
}

impl HousingBuilder {
    fn main_body(&self) -> SdfModel {
        let mut sdf = SdfModel::new();
        sdf.add_sdf(
            &self.aabb.as_sdf().difference(
                &Cylinder::new(
                    Vec3::new(0.0, 0.0, self.back_thickness),
                    Vec3::axis_z() * self.inf,
                    self.drum_bounding_radius,
                )
                .as_sdf(),
            ),
        );
        sdf.subtract_sdf(
            &Aabb::new(
                Vec3::new(-self.inf, self.catch.bottom_y, self.back_thickness),
                Vec3::new(self.catch.indent_x, 0.0, self.inf),
            )
            .as_sdf(),
        );
        sdf
    }
    fn mount(&self, sdf: &mut SdfModel, y: f64) {
        sdf.add_sdf(
            &TruncatedCone::new(
                Vec3::new(self.mount.off_x, y, self.back_thickness),
                Vec3::new(0.0, 0.0, self.mount.length),
                self.mount.rad1,
                self.mount.rad2,
            )
            .as_sdf(),
        );
        sdf.drill_ruthex(
            Vec3::new(self.mount.off_x, y, self.back_thickness + self.mount.length),
            -Vec3::axis_z(),
            &THREAD_M3,
        );
        sdf.add_sdf(
            &Cylinder::new(
                Vec3::new(self.mount.off_x, 0.0, self.back_thickness),
                Vec3::new(0.0, 0.0, self.mount.extra_back),
                self.mount.motor_radius + self.mount.motor_fit,
            )
            .as_sdf(),
        );
    }
    fn brace_x(&self, y: f64, dy: f64) -> Sdf3 {
        let mut sdf = Sdf::empty();
        sdf = sdf.union(
            &Polygon2::new(vec![
                Vec2::new(
                    y + dy * (self.mount.rad2 - self.brace.indent),
                    self.back_thickness,
                ),
                Vec2::new(
                    y + dy * (self.mount.rad2 - self.brace.indent + self.brace.extent),
                    self.back_thickness,
                ),
                Vec2::new(
                    y + dy * (self.mount.rad2 - self.brace.indent),
                    self.back_thickness + self.mount.length,
                ),
            ])
            .as_sdf()
            .extrude_x(
                self.mount.off_x - self.brace.width / 2.0
                    ..self.mount.off_x + self.brace.width / 2.0,
            ),
        );
        sdf
    }
    fn brace_y(&self, y: f64, dx: f64) -> Sdf3 {
        let mut sdf = Sdf::empty();
        sdf = sdf.union(
            &Polygon2::new(vec![
                Vec2::new(
                    self.mount.off_x + dx * (self.mount.rad2 - self.brace.indent),
                    self.back_thickness,
                ),
                Vec2::new(
                    self.mount.off_x
                        + dx * (self.mount.rad2 - self.brace.indent + self.brace.extent),
                    self.back_thickness,
                ),
                Vec2::new(
                    self.mount.off_x + dx * (self.mount.rad2 - self.brace.indent),
                    self.back_thickness + self.mount.length,
                ),
            ])
            .as_sdf()
            .extrude_y(-y - self.brace.width / 2.0..-y + self.brace.width / 2.0),
        );
        sdf
    }
    fn mounts(&self, sdf: &mut SdfModel) {
        self.mount(sdf, self.mount.off_y);
        self.mount(sdf, -self.mount.off_y);
    }
    fn wiring_pos(&self) -> Sdf3 {
        let mut sdf = Sdf::empty();
        sdf = sdf.union(
            &Polygon2::new(vec![
                Vec2::new(
                    self.tube.width / 2.0 - self.tube.wire_inlet1,
                    self.tube.wall_bottom,
                ),
                Vec2::new(
                    self.tube.width / 2.0 - self.tube.wire_inlet1 - self.tube.tab_width,
                    self.tube.wall_bottom,
                ),
                Vec2::new(
                    self.tube.width / 2.0 - self.tube.wire_inlet1 - self.tube.tab_width,
                    self.back_thickness - self.tube.wall_top - self.tube.wire_inlet2,
                ),
            ])
            .as_sdf()
            .extrude_x(self.hall_port.start_x + self.hall_port.width..self.aabb.max().x()),
        );
        sdf
    }
    fn wiring_neg(&self) -> Sdf3 {
        let mut sdf = Sdf::empty();
        sdf = sdf.union(
            &Aabb::new(
                Vec3::new(
                    self.hall_port.start_x + self.hall_port.width,
                    -self.tube.width / 2.0,
                    self.tube.wall_bottom,
                ),
                Vec3::new(
                    self.inf,
                    self.tube.width / 2.0,
                    self.back_thickness - self.tube.wall_top,
                ),
            )
            .as_sdf(),
        );
        sdf = sdf.union(
            &Aabb::new(
                Vec3::new(
                    self.hall_port.start_x + self.hall_port.width,
                    self.tube.width / 2.0 - self.tube.wire_inlet1,
                    -self.inf,
                ),
                Vec3::new(
                    self.inf,
                    self.tube.width / 2.0,
                    (self.tube.wall_bottom + self.back_thickness - self.tube.wall_top) / 2.0,
                ),
            )
            .as_sdf(),
        );
        sdf
    }
    fn port_neg(&self) -> Sdf3 {
        Aabb::new(
            Vec3::new(self.port.start_x, -self.port.length / 2.0, -self.inf),
            Vec3::new(
                self.port.start_x + self.port.width,
                self.port.length / 2.0,
                self.inf,
            ),
        )
        .as_sdf()
        .union(
            &Aabb::new(
                Vec3::new(
                    self.hall_port.start_x,
                    self.hall_port.start_y - self.hall_port.length / 2.0,
                    -self.inf,
                ),
                Vec3::new(
                    self.hall_port.start_x + self.hall_port.width,
                    self.hall_port.start_y + self.hall_port.length / 2.0,
                    self.inf,
                ),
            )
            .as_sdf(),
        )
    }
    fn hall_mount(&self, sdf: &mut SdfModel) {
        let norm = Vec2::from_deg(self.hall_mount.tilt_deg);
        let norm = Vec3::new(0.0, norm.x(), norm.y());
        sdf.add_sdf(
            &Aabb::new(
                Vec3::new(
                    self.hall_mount.hole1_x
                        - self.hall_mount.width
                        - self.hall_mount.thickness / 2.0,
                    self.hall_mount.off_y - self.hall_mount.thickness / 2.0,
                    self.back_thickness,
                ),
                Vec3::new(
                    self.hall_mount.hole1_x + self.hall_mount.thickness / 2.0,
                    self.hall_mount.off_y + self.hall_mount.thickness / 2.0,
                    self.back_thickness + self.hall_mount.length,
                ),
            )
            .as_sdf()
            .union(
                &TruncatedCone::new(
                    Vec3::new(
                        self.hall_mount.hole1_x,
                        self.hall_mount.off_y,
                        self.back_thickness,
                    ),
                    Vec3::axis_z() * (self.hall_mount.length + self.hall_mount.extra_cone),
                    self.hall_mount.rad1,
                    self.hall_mount.rad2,
                )
                .as_sdf(),
            )
            .union(
                &TruncatedCone::new(
                    Vec3::new(
                        self.hall_mount.hole1_x - self.hall_mount.width,
                        self.hall_mount.off_y,
                        self.back_thickness,
                    ),
                    Vec3::axis_z() * (self.hall_mount.length + self.hall_mount.extra_cone),
                    self.hall_mount.rad1,
                    self.hall_mount.rad2,
                )
                .as_sdf(),
            )
            .difference(
                &Plane::new(
                    Vec3::new(
                        0.0,
                        self.hall_mount.off_y + self.hall_mount.hole_bias,
                        self.back_thickness + self.hall_mount.length,
                    ),
                    -norm,
                )
                .as_sdf(),
            ),
        );
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
async fn main() -> anyhow::Result<()> {
    let tabs = Tabs::new();
    HousingBuilder {
        inf: 1000.0,
        aabb: Aabb::new(
            Vec3::new(tabs.aabb.min().x(), tabs.aabb.min().y(), 0.0),
            Vec3::new(tabs.aabb.max().x(), tabs.aabb.max().y(), 50.0),
        ),

        drum_bounding_radius: 52.0,
        back_thickness: 4.0,
        tabs: Tabs::new(),
        catch: Catch {
            bottom_y: -56.0,
            indent_x: -15.0,
        },
        mount: Mount {
            off_x: 8.0,
            off_y: 17.5,
            length: 22.2,
            motor_radius: 14.0,
            motor_fit: 0.05,
            rad1: 8.0,
            rad2: 5.0,
            extra_back: 4.0,
        },
        brace: Brace {
            width: 2.0,
            extent: 6.0,
            indent: 0.2,
        },
        port: Port {
            start_x: 16.0,
            width: 7.0,
            length: 16.0,
        },
        hall_port: HallPort {
            start_x: -16.0,
            start_y: 0.0,
            width: 5.0,
            length: 16.0,
        },
        tube: Tube {
            width: 14.0,
            wall_bottom: 0.6,
            wall_top: 0.8,
            wire_inlet1: 2.0,
            wire_inlet2: 2.0,
            tab_width: 2.0,
        },
        hall_mount: HallMount {
            width: 10.0,
            thickness: 6.0,
            length: 20.0,
            hole1_x: -9.0,
            off_y: -13.0,
            rad1: 4.0,
            rad2: 4.0,
            tilt_deg: 60.0,
            extra_cone: 2.0,
            hole_bias: 2.0,
        },
        drum_guide: DrumGuide {
            length: 20.0,
            rad_inner: 53.0 / 2.0,
            rad_outer: 55.0 / 2.0,
            seam_cut_width: 2.0,
            seam_cut_depth: 0.3,
        },
        top_catch: TopCatch {
            min_y: 35.0,
            max_y: 50.0,
            thickness: 2.0,
        },
        board_mounts: BoardMounts {
            standoff: 5.0,
            thread: &THREAD_M2,
            brace_width: 3.0,
            brace_inset: 0.5,

            board1_vertical: 15.0,
            board2_vertical: 25.0,
            board_width: 43.0,
            board_height: 29.0,
            board_offset_z: 0.0,
        },
        vertical_mounts: VerticalMounts {
            height: 12.0,
            thread: &THREAD_M3,
        },
    }
    .build()
    .await?;
    Ok(())
}

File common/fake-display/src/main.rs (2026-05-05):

#![deny(unused_must_use)]
#![allow(unused_imports)]
#![allow(unreachable_code)]
#![allow(unused_variables)]

use arena::Arena;
use clap::Parser;
use clap::builder::TypedValueParser;
use embassy_futures::select::select4;
use embassy_futures::select::{Either4, Either5, select5};
use embassy_sync::blocking_mutex::raw::NoopRawMutex;
use glyph_render::Renderer;
use io_adapters::split::split_io;
use io_adapters::tokio::TokioStreamAdapter;
use mqtt_client::client::{ConnectRequest, MqttClient, PublishRequest};
use mqtt_core::protocol::{Packet, Qos};
use protocol::display::MAX_GLYPH_BYTES;
use protocol::display::MAX_GLYPHS;
use protocol::display::{DisplayRequest, DisplayResponse};
use protocol::setup::DeviceInfo;
use rustls::pki_types::ServerName;
use serde_json_core::heapless;
use serde_json_core::heapless::CapacityError;
use std::env;
use std::future::pending;
use std::sync::Arc;
use std::time::Duration;
use tokio::net::TcpStream;
use tokio_rustls::TlsConnector;

#[derive(Parser, Debug)]
#[command(version, about, long_about = None)]
struct Args {
    #[arg(long)]
    mqtt_host: String,
    #[arg(long)]
    mqtt_port: u16,
    #[arg(long)]
    mqtt_client_id: String,
    #[arg(long)]
    mqtt_username: String,
    #[arg(long)]
    mqtt_password: String,
    #[arg(long)]
    mqtt_topic: String,
    #[arg(long)]
    glyph_count: usize,
    #[arg(long)]
    background_color: String,
    #[arg(long)]
    foreground_color: String,
}

const KEEPALIVE: u16 = 60;

const GLYPHS: &[&str] = &[
    " ", "A", "B", "C", "D", "E", "F", "G", "H", "I", "J", "K", "L", "M", "N", "O", "P", "Q", "R",
    "S", "T", "U", "V", "W", "X", "Y", "Z", "$", "&", "#", "0", "1", "2", "3", "4", "5", "6", "7",
    "8", "9", ":", ".", "-", "?", "!",
];

#[tokio::main]
async fn main() -> anyhow::Result<()> {
    let args = Args::parse();
    let mut root_cert_store = rustls::RootCertStore::empty();
    root_cert_store.extend(webpki_roots::TLS_SERVER_ROOTS.iter().cloned());
    let config = rustls::ClientConfig::builder()
        .with_root_certificates(root_cert_store)
        .with_no_client_auth();
    let connector = TlsConnector::from(Arc::new(config));
    let stream = TcpStream::connect((args.mqtt_host.clone(), args.mqtt_port))
        .await
        .unwrap();
    let stream = connector
        .connect(ServerName::try_from(args.mqtt_host).unwrap(), stream)
        .await
        .unwrap();
    let (read, write) = split_io(stream);
    let client = MqttClient::<NoopRawMutex, _, _, 1024, 1, 1>::new(
        TokioStreamAdapter(write),
        TokioStreamAdapter(read),
    );
    let (request_send, mut request_recv) = tokio::sync::mpsc::unbounded_channel::<DisplayRequest>();
    let req_topic = format!("{}/request", args.mqtt_topic);
    let resp_topic = format!("{}/response", args.mqtt_topic);
    let info_topic = format!("{}/info", args.mqtt_topic);
    match select4(
        async {
            println!("Connecting...");
            client
                .connect(&ConnectRequest {
                    client_id: "sfasfgasfgf",
                    username: Some(&args.mqtt_username),
                    password: Some(&args.mqtt_password),
                    keepalive: KEEPALIVE,
                })
                .await?;
            println!("Subscribing...");
            client.subscribe(&req_topic).await?;
            println!("Publishing Device Info...");
            let device_info: heapless::Vec<u8, 1024> = serde_json_core::to_vec(&DeviceInfo {
                serial: 0,
                git_version: Default::default(),
                git_dirty: None,
                git_head_ref: Default::default(),
                glyphs: args.glyph_count,
                background: (*args.background_color).try_into()?,
                foreground: (*args.foreground_color).try_into()?,
            })?;
            client
                .publish(&PublishRequest {
                    qos: Qos::AtMostOnce,
                    topic: &info_topic,
                    payload: &device_info,
                    retain: true,
                })
                .await?;
            println!("Ready");
            pending::<()>().await;
            anyhow::Result::<()>::Ok(())
        },
        async {
            let mut tmp = [0u8; 1024];
            let mut arena = [0u8; 1024];
            loop {
                let arena = Arena::new(&mut arena)?;
                let (token, packet): (_, Packet) = client.receive(arena).await?;
                match packet {
                    Packet::Publish(packet) => {
                        let request = serde_json_core::from_slice_escaped::<DisplayRequest>(
                            &packet.payload,
                            &mut tmp,
                        )?
                        .0;
                        request_send.send(request)?;
                    }
                    _ => {}
                }
                client.acknowledge(token)?;
            }
            anyhow::Result::<()>::Ok(())
        },
        async {
            loop {
                tokio::time::sleep(Duration::from_secs(KEEPALIVE as u64)).await;
                client.ping().await?;
            }
            anyhow::Result::<()>::Ok(())
        },
        async {
            while let Some(next) = request_recv.recv().await {
                match next {
                    DisplayRequest::Run(a) => {
                        let glyphs = GLYPHS.iter().map(|x| &**x).collect::<Vec<_>>();
                        let mut renderer = Renderer::<MAX_GLYPHS>::new(&glyphs);
                        renderer.append(&a)?;
                        let rendered = renderer.finish();
                        let rendered:heapless::Vec<heapless::String<MAX_GLYPH_BYTES>,MAX_GLYPHS> =
                            rendered
                                .iter()
                                .map(|x| {
                                    heapless::String::<MAX_GLYPH_BYTES>::try_from(&*GLYPHS[*x])
                                })
                                .collect::<Result<
                                    Vec<heapless::String<MAX_GLYPH_BYTES>>,
                                    CapacityError,
                                >>()?
                                .try_into()?;
                        println!("Rendered = {:?}", rendered);
                        client
                            .publish(&PublishRequest {
                                qos: Qos::AtMostOnce,
                                topic: &resp_topic,
                                payload: &serde_json_core::to_vec::<_, 1024>(
                                    &DisplayResponse::Start(rendered.clone()),
                                )?,
                                retain: false,
                            })
                            .await?;
                        tokio::time::sleep(Duration::from_secs(2)).await;
                        client
                            .publish(&PublishRequest {
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

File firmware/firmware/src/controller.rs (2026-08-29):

use crate::driver::DriverModule;
use crate::error::Error;
use core::cell::RefCell;
use core::default::Default;
use core::ops::Index;
use core::{fmt, iter};
use embassy_sync::blocking_mutex::raw::NoopRawMutex;
use embassy_sync::mutex::{Mutex, MutexGuard};
use embassy_time::{Instant, Timer};
use heapless::{CapacityError, String, Vec};
use log::{error, info};
use make_static::make_static;
use protocol::display::{MAX_GLYPHS, STEPS_PER_REVOLUTION};
use protocol::setup::{DisplaySettings, DriverVersion};

const MODULE: &'static str = "[CTRL ]";
const FLAP_COUNT: usize = 45;
#[derive(Debug, Copy, Clone, Eq, PartialEq)]
enum SegmentMode {
    Disabled,
    Spinning,
    Decelerating,
    Holding(usize),
}
#[derive(Debug)]
pub struct SegmentController {
    target: isize,
    position: isize,

    prev_hall: Option<bool>,
    homed: bool,

    phase: usize,
    mode: SegmentMode,
    ticks_until_step: usize,
    accel_step: usize,
}

pub struct DisplayController {
    driver: &'static DriverModule,
    segments: Vec<SegmentController, MAX_GLYPHS>,
}

pub struct DisplayControllerGuard<'a> {
    settings: DisplaySettings,
    guard: MutexGuard<'a, NoopRawMutex, DisplayController>,
}

pub struct ControllerModule {
    display: Mutex<NoopRawMutex, DisplayController>,
    settings: RefCell<DisplaySettings>,
}

impl ControllerModule {
    pub fn set_settings(&self, settings: DisplaySettings) {
        *self.settings.borrow_mut() = settings;
    }
}

impl<'a> Drop for DisplayControllerGuard<'a> {
    fn drop(&mut self) {
        for segment in &mut self.guard.segments {
            segment.mode = SegmentMode::Disabled;
        }
        self.guard.driver.set_enabled(false);
    }
}

impl ControllerModule {
    pub fn new(driver: &'static DriverModule) -> &'static Self {
        make_static!(
            ControllerModule,
            ControllerModule {
                display: Mutex::new(DisplayController {
                    driver,
                    segments: Vec::new()
                }),
                settings: RefCell::new(DisplaySettings::default()),
            }
        )
    }
    async fn enable(&self) -> DisplayControllerGuard<'_> {
        let mut guard = self.display.lock().await;
        guard.driver.set_enabled(true);
        DisplayControllerGuard {
            settings: self.settings.borrow().clone(),
            guard,
        }
    }
    pub async fn run(&self, message: &[usize]) -> Result<(), Error> {
        Ok(self.enable().await.run(message).await?)
    }
}

impl SegmentController {
    fn advance(&mut self) {
        self.position += 1;
        self.phase = (self.phase + 1) % 4;
    }
}

struct AccelerationCurve {
    micros_per_tick: u64,
    ticks_per_step: Vec<u8, 1024>,
}

struct AccelerationStage {
    ticks_per_step: u32,
    steps_per_stage: u32,
}

impl AccelerationCurve {
    pub fn new(settings: &DisplaySettings) -> Result<AccelerationCurve, Error> {
        let micros_per_tick = settings.micros_per_tick.unwrap_or(350);
        let slow_ticks_per_step = settings.slow_ticks_per_step.unwrap_or(3);
        let fast_ticks_per_step = settings.fast_ticks_per_step.unwrap_or(6);
        let slow_steps_per_stage = settings.slow_steps_per_stage.unwrap_or(6);
        let mut ticks_per_step_vec = Vec::new();
        let slow_ticks_per_step_1 = slow_ticks_per_step as f32;
        let slow_ticks_per_step_2 = slow_ticks_per_step_1 * slow_ticks_per_step_1;
        let slow_ticks_per_step_4 = slow_ticks_per_step_2 * slow_ticks_per_step_2;
        for ticks_per_step in (fast_ticks_per_step + 1..=slow_ticks_per_step).rev() {
            // This formula delivers approximately constant mechanical power.
            let ticks_per_step_1 = ticks_per_step as f32;
            let ticks_per_step_2 = ticks_per_step_1 * ticks_per_step_1;
            let ticks_per_step_4 = ticks_per_step_2 * ticks_per_step_2;
            let steps_per_stage =
                ((slow_steps_per_stage as f32) * slow_ticks_per_step_4 / ticks_per_step_4) as u32;
            for i in 0..steps_per_stage {
                ticks_per_step_vec
                    .push(ticks_per_step)
                    .map_err(|_| Error::CapacityError)?;
            }
        }
        ticks_per_step_vec
            .push(fast_ticks_per_step)
            .map_err(|_| Error::CapacityError)?;
        Ok(AccelerationCurve {
            micros_per_tick,
            ticks_per_step: ticks_per_step_vec,
        })
    }
}

impl<'a> DisplayControllerGuard<'a> {
    async fn run(&mut self, message: &[usize]) -> Result<(), Error> {
        self.recount()?;
        self.set_targets(message);
        self.drive_all_to_targets(message).await?;
        Ok(())
    }
    fn recount(&mut self) -> Result<(), Error> {
        let count = self.guard.driver.count()?;
        if count > MAX_GLYPHS {
            return Err(Error::CapacityError);
        }
        while self.guard.segments.len() > count {
            self.guard.segments.pop();
        }
        while self.guard.segments.len() < count {
            self.guard
                .segments
                .push(SegmentController {
                    target: 0,
                    position: 0,
                    prev_hall: None,
                    homed: false,
                    phase: 0,
                    mode: SegmentMode::Disabled,
                    ticks_until_step: 0,
                    accel_step: 0,
                })
                .ok()
                .unwrap();
        }
        Ok(())
    }
    fn set_targets(&mut self, message: &[usize]) {
        for (index, char) in self.guard.segments.iter_mut().enumerate() {
            let calibration = self.settings.calibration.get(index).cloned().unwrap_or(0);
            let new_target = ((calibration
                + message.get(index).cloned().unwrap_or(0) * STEPS_PER_REVOLUTION / FLAP_COUNT)
                % STEPS_PER_REVOLUTION) as isize;
            if !char.homed || new_target != char.position {
                char.target = new_target;
                char.mode = SegmentMode::Spinning;
                char.accel_step = 0;
                if self.settings.rehome_after_stopping {
                    char.homed = false;
                    char.position = 0;
                }
            }
        }
    }
    fn write_to_drivers(&mut self) -> Result<(), Error> {
        let reverse = match self.settings.driver_version {
            DriverVersion::V1_0 => true,
            DriverVersion::V2_0 => false,
        };
        let mut output_buffer = Vec::<u8, { (MAX_GLYPHS + 1) / 2 }>::new();
        for cs in self.guard.segments.chunks_mut(2) {
            let mut b = 0;
            for (i, c) in cs.iter_mut().enumerate() {
                let mut mask = 0;
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

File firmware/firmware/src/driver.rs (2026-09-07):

use crate::error::Error;
use core::cell::RefCell;
use cortex_m::asm::delay;
use embassy_futures::yield_now;
use embassy_rp::gpio::{Level, Output, SlewRate};
use embassy_rp::peripherals::{PIN_0, PIN_1, PIN_2, PIN_3, PIN_4, PIN_5, PIN_6, SPI0};
use embassy_rp::pwm::Pwm;
use embassy_rp::spi::{Blocking, Spi};
use embassy_rp::{Peri, spi};
use embassy_time::{Delay, Timer};
use embedded_hal::delay::DelayNs;
use embedded_hal::digital::OutputPin;
use log::{error, info};
use error_report::Report;
use make_static::make_static;

const MODULE: &str = "[DRIVE]";

#[allow(non_snake_case)]
pub struct DriverPeripherals {
    /// CIPO
    pub PIN_0: Peri<'static, PIN_0>,
    /// LATCH
    pub PIN_1: Peri<'static, PIN_1>,
    /// GND
    pub GND1: (),
    /// CLOCK
    pub PIN_2: Peri<'static, PIN_2>,
    /// COPI
    pub PIN_3: Peri<'static, PIN_3>,
    /// LOAD
    pub PIN_4: Peri<'static, PIN_4>,
    /// RESET or FAULT
    pub PIN_5: Peri<'static, PIN_5>,
    /// GND
    pub GND2: (),
    /// ENABLE
    pub PIN_6: Peri<'static, PIN_6>,
    /// SPI
    pub SPI0: Peri<'static, SPI0>,
}
struct DriverInner {
    spi: Spi<'static, Blocking>,
    load: Output<'static>,
    latch: Output<'static>,
    enable: Output<'static>,
}
pub struct DriverModule {
    inner: RefCell<DriverInner>,
}

impl DriverModule {
    pub fn set_enabled(&self, enabled: bool) {
        let ref mut inner = *self.inner.borrow_mut();
        if enabled {
            inner.enable.set_low();
        } else {
            inner.enable.set_high();
        }
    }
    pub fn count(&self) -> Result<usize, Error> {
        let ref mut inner = *self.inner.borrow_mut();
        inner.load.set_low();
        Delay.delay_us(10);
        inner.load.set_high();
        Delay.delay_us(10);
        for count in 0usize..20 {
            let mut data = [0u8];
            inner.spi.blocking_read(&mut data)?;
            if data[0] == 0xFF {
                // info!("{MODULE} Counted {} flaps", count);
                return Ok(count);
            } else {
                if data[0] != 0b01 && data[0] != 0b11 {
                    // info!("Bad data {:?}", data);
                }
            }
        }
        Err(Error::CountFailure)
    }
    pub fn write(&self, data: &[u8]) -> Result<(), Error> {
        let ref mut inner = *self.inner.borrow_mut();
        inner.spi.blocking_write(data)?;
        inner.latch.set_low();
        Delay.delay_us(10);
        inner.latch.set_high();
        Delay.delay_us(10);
        Ok(())
    }
    pub fn read(&self, data: &mut [u8]) -> Result<(), Error> {
        let ref mut inner = *self.inner.borrow_mut();
        inner.load.set_low();
        Delay.delay_us(10);
        inner.load.set_high();
        Delay.delay_us(10);
        inner.spi.blocking_read(data)?;
        Ok(())
    }
}

impl DriverModule {
    pub async fn new(peri: DriverPeripherals) -> Result<&'static DriverModule, Error> {
        let mut config = spi::Config::default();
        config.frequency = 1000000;
        let mut spi = Spi::new_blocking(peri.SPI0, peri.PIN_2, peri.PIN_3, peri.PIN_0, config);
        let mut load = Output::new(peri.PIN_4, Level::High);
        let mut latch = Output::new(peri.PIN_1, Level::High);
        let mut enable = Output::new(peri.PIN_6, Level::High);

        let module = make_static!(
            DriverModule,
            DriverModule {
                inner: RefCell::new(DriverInner {
                    spi,
                    load,
                    latch,
                    enable,
                }),
            }
        );
        Ok(module)
    }
    pub async fn run_read_test(&self) {
        loop {
            let mut buf = [0u8; 20];
            if let Err(e) = self.read(&mut buf) {
                error!("error during read test: {}", Report::new(e));
                return;
            }
            info!("read = {:?}", buf);
            Timer::after_millis(100).await;
        }
    }
}

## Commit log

2025-06-13 First commit.
    [all flaps.3mf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]
2025-08-05 Added models.
    [all flaps.3mf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]
2025-08-22 Added controller.
    [driver.kicad_sch]
2025-09-23 Start to implement controller and driver.
    [driver-B_Cu.gbl, driver-B_Mask.gbs, driver-B_Paste.gbp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]
2025-10-07 Implement driver.
    [BOM-driver2.csv, PW0016A.stl, PW0016A.stp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]
2025-10-09 Increase size of walls around ruthex thread holes.
    [flaps.3mf, housing.3mf, outer.3mf]
2025-10-10 Enable elephant's foot compensation.
    [flaps.3mf, housing.3mf, outer.3mf]
2025-10-31 Bug fixes.
    [flaps.3mf, housing.3mf, outer.3mf]
2025-11-19 Start implementing pico controller.
    [flaps.3mf, inner.3mf]
2025-11-24 Actually run the motors
2025-12-03 Add second driver and implement preemptive execution for logginn
    [QFN-24_MP6605C_MNP.step, driver3.kicad_pcb, driver3.kicad_sch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]
2025-12-05 Add new driver and web client
    [BOM-driver3.csv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]
2025-12-11 Create workspace for pico
2025-12-11 Rename controller-pico
2025-12-15 Go back to DRV8804 based design because the MP6605CGR seems to be out of stock.
    [BOM-driver3.csv, DYY0016A.stp, PWP0016J.stp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]
2025-12-18 Add picotool reset support.
    [BOM-driver3.csv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]
2025-12-18 Refactor directory structure for releases.
    [BOM-driver2.csv, BOM-driver3.csv, PW0016A.stl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]
2025-12-18 Add missed changes.
    [DYY0016A.stp, PWP0016J.stp, QFN-24_MP6605C_MNP.step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]
2025-12-18 Fix build for models.
    [flaps.3mf, housing.3mf, inner.3mf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]
2025-12-19 Setup over USB
    [driver.kicad_pcb]
2025-12-22 Update gitignore
    [flaps.3mf, housing.3mf, inner.3mf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]
2025-12-22 Add more detailed error codes.
    [lib.rs]
2025-12-24 Implemented fixed certificate verification.
    [application.rs, lib.rs, main.rs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]
2025-12-25 Retain DeviceInfo MQTT response and slow down spi communication with radio.
2025-12-29 Update magnet size and fitment. Larger magnets allow for worse tolerances in the hall sensor.
2025-12-31 Housing: * Move attachment tabs to top and bottom only. * Route hall sensor wires under motor. * Shrink radius for wheel * Shrink housing slightly * Set up PCB mounts for new PCBs. * Add screw holes 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
2025-12-31 Fix alignment of hall port.
    [housing.rs]
2026-01-20 Widen flanges to fit more tightly in housing
2026-01-20 Retain DeviceInfo and display content
2026-01-21 Fix data loss in BLE transmissions due to deadlock.
    [application.rs, radio.rs]
2026-01-23 Make glyph list configurable.
    [driver.kicad_pcb, driver.kicad_sch]
2026-01-23 Pin toolchain version to handle compilation errors.
2026-01-23 Fix try block inferefence issue.
    [application.rs]
2026-01-23 Remove use of broken static_cell macro and bump rust version.
    [application.rs, driver.rs, lib.rs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]
2026-01-25 Add spindle submodule.
2026-01-26 Adjust fitment of drum inside housing.
2026-01-26 Add hall effect sensor test.
2026-01-28 Add spindle interpreter.
2026-01-28 Tune filament flow ratio for flaps.
2026-01-28 Fix issue with duplicate filament settings id.
2026-01-29 Tune flow ratio.
2026-01-29 Update display controller for new drivers.
2026-01-30 Create more room for hall cable to route, and enable brim.
2026-01-30 Add brim points to housing.
2026-02-03 Implement spindle compiler.
2026-02-12 integrate spindle into firmware.
2026-02-12 Fix issues with spindle code.
    [application.rs, controller.rs, spindle.rs]
2026-02-13 Interrupt previous request for new request.
2026-02-14 Faster motor controller.
2026-02-15 Fix variable indices with multiple function arguments.
    [spindle.rs]
2026-02-17 Switch to block and instruction based interp.
2026-02-18 Limit lifetime capture in errors to allow longer-lasting errors.
    [lib.rs]
2026-02-19 Add short-circuit boolean operators.
2026-02-20 Implement acceleration and deceleration in motor controller.
2026-02-27 Add backing for flap holes to reduce bed adhesion issues.
2026-04-02 Add tabs based on buttons.
2026-04-11 Add bootsel button reading support.
2026-04-11 Wait for button press before accepting bluetooth connection.
2026-04-11 Implement some callback binding helpers.
    [lib.rs]
2026-04-12 Fix warnings and add missing nusb dependency.
    [main.rs]
2026-04-15 Fix bluetooth on wasm.
    [lib.rs, main.rs]
2026-04-15 Fix crashes when USB is not supported.
    [lib.rs]
2026-04-16 Fix build with feature powerset and release scripts.
    [application.rs, lib.rs, main.rs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]
2026-04-21 Switch from embassy_executor::task to LocalSpawn for easier capture.
2026-04-28 Move error conversions into from impls with feature gates.
    [lib.rs]
2026-05-01 Use core::error::Error through error tree.
    [application.rs, controller.rs, driver.rs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]
2026-05-05 Create calibration editor.
2026-05-08 Instruct user to restart device if connecting to picoboot from setup tab.
2026-05-29 Start work on driver v3.
    [DYY0016A.stp, PWP0016J.stp, QFN-24_MP6605C_MNP.step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]
2026-06-15 Optimize driver3 size and re-add spin test to firmware.
    [driver.kicad_pcb, driver.kicad_sch, drv.kicad_sch]
2026-06-20 Increase cable tube size to accomodate larger cables.
